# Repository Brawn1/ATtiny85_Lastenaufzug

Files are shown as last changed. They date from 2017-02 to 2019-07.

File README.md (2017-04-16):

# RF AtTiny85 gesteuerter Lastenaufzug

**Anleitung in Arbeit**

Da wir gerne Grillen aber die Sachen vom 1.OG jedesmal hinunter und 
wieder rauftragen müssen, haben wir uns entschlossen 
eine Seilwinde die noch in der Garage lag unter dem Balkon im 2.OG zu 
montieren.

Die Montage war einfach, aber leider stellte sich heraus das die 
Seilwinde sehr Langsam ist, und man die nur mit einem 2m Kabel vom 1.OG 
bedienen konnte.

Also habe ich mir überlegt dies per Microcontroller über Funk zu 
Steuern.

Da der Microcontroller keine hohe Lasten schalten kann, Steuere ich 
damit 2 Wechselrelais an.
Die Relais werden auf der 230VAC Seite so verdrahtet, dass auch bei 
einem Stecken von einem Relais immer nur eines aktiv sein kann.
Ob das jetzt das Relais für Rauf oder Runter ist kommt von der 
Sicherheit darauf an (bei mir ist es Rauf da sonst der Motor keinen
Abschaltpunkt hat).

**Tipp:**
Wenn man mehr Geld Investieren möchte, wäre ein Sicherheitsrelais 
(Schütz) dafür besser vorgesehen. Da es aber Privat ist und der 
Lastenaufzug gerade mal ca. 10x im Jahr genutzt wird, ist das nicht so 
schlimm. (über Winter wird es vom Netz getrennt).

Damit auch der Lastenaufzug vor Ort Manuell bedient werden kann, sind 
auch noch 2 Taster (Rauf, Runter) am Kasten montiert.

Da es sehr viel mit 433Mhz Fernbedinung gibt, habe ich zuerst den Code 
von der FB Ausgelesen und es in die Konditionen im Loop eingebaut.
Zum Empfangen hat sich die Lib RC-Switch am besten bewährt.

Da die Relais eher Träge sind, wird zur Sicherheit zwischen dem 
Umschalten 80ms gewartet.
Es würde zwar durch die Verdrahtung nichts machen wenn beide Relais 
aktiv sind, aber man muss es ja nicht fordern.

Kurze Funktionsvorführung

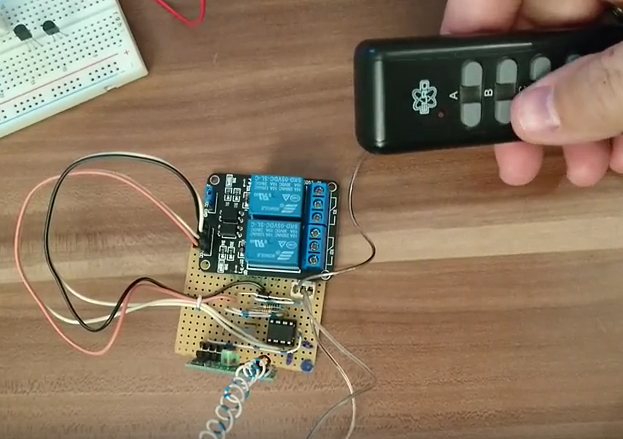
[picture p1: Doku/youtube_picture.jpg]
Funktionstest (https://youtu.be/YJzWT5fqY5Q)


Werde ein Video dazu noch nachreichen, sobald es etwas Wärmer ist. ;-)

## Benötigte Teile

* 1x 433Mhz Empfänger (E-Bay um ca. 2,50 € (Sender & Empfänger)
* 1x AtTiny85 (für die Steuerung)
* 1x Transistor PNP
* 1x 800 Ohm Widerstand
* 1x 2-Fach Relais (Bei E-Bay um ca. 5 €) *Achtung: ich habe aus 
versehen die Relais mit Optokopler gekauft, somit muss ich zum 
Abschalten der Relais die Ports auf HIGH setzen.*

## Verdrahtung

Die Verdrahtung ist dank dem AtTiny85 sehr einfach.

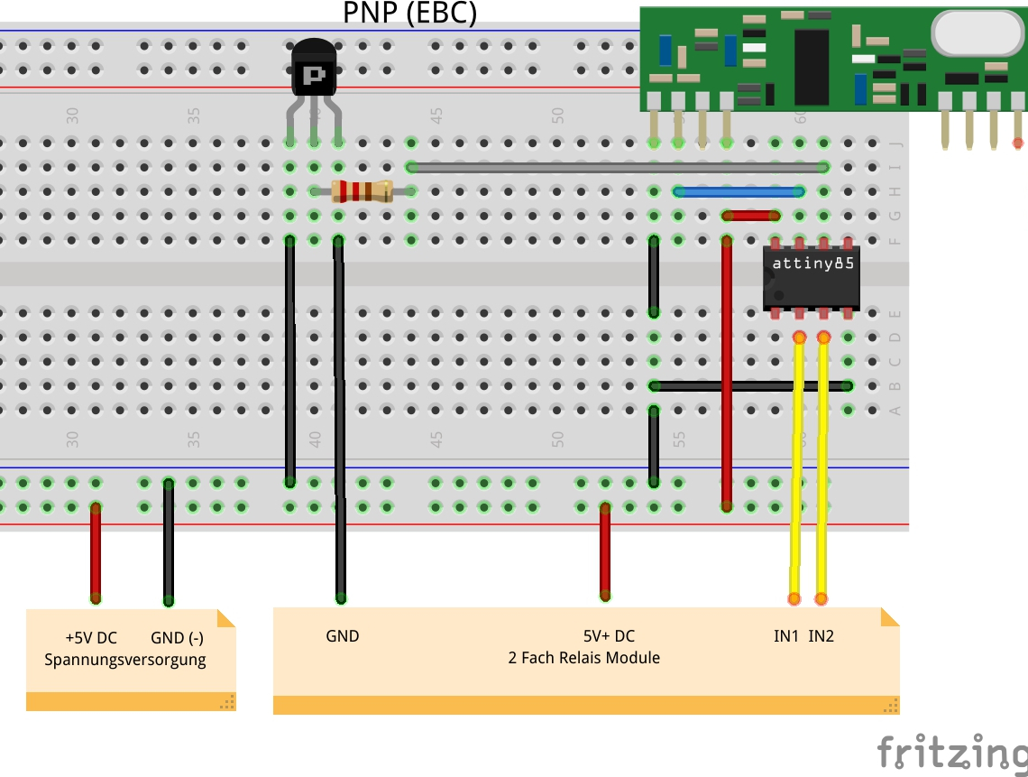
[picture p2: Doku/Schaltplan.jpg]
Verdrahtung AtTiny85

Wie man sieht verwende ich einen Widerstand von ca. 800 Ohm für den 
Transistor, somit habe ich für die Relais genau 5,5VDC.

So als Startpunkt sollte man einen 1KOhm Widerstand verwenden und es mit 
einem Multimeter nachmessen.

---

**Die Pins vom AtTiny85 werden wie dargestellt verwendet:**

---

* *PB1* -> aktivierung Spannungsversorgung vom Relais über PNP Transistor
* *PB2* -> *DATA* RF-Empfänger
* *PB3* -> *IN1* Relais 1
* *PB4* -> *IN2* Relais 2
* *VIN* -> max. 5,5 VDC
* *GND* -> GND

**433 Mhz Empfänger Aufgelötet**
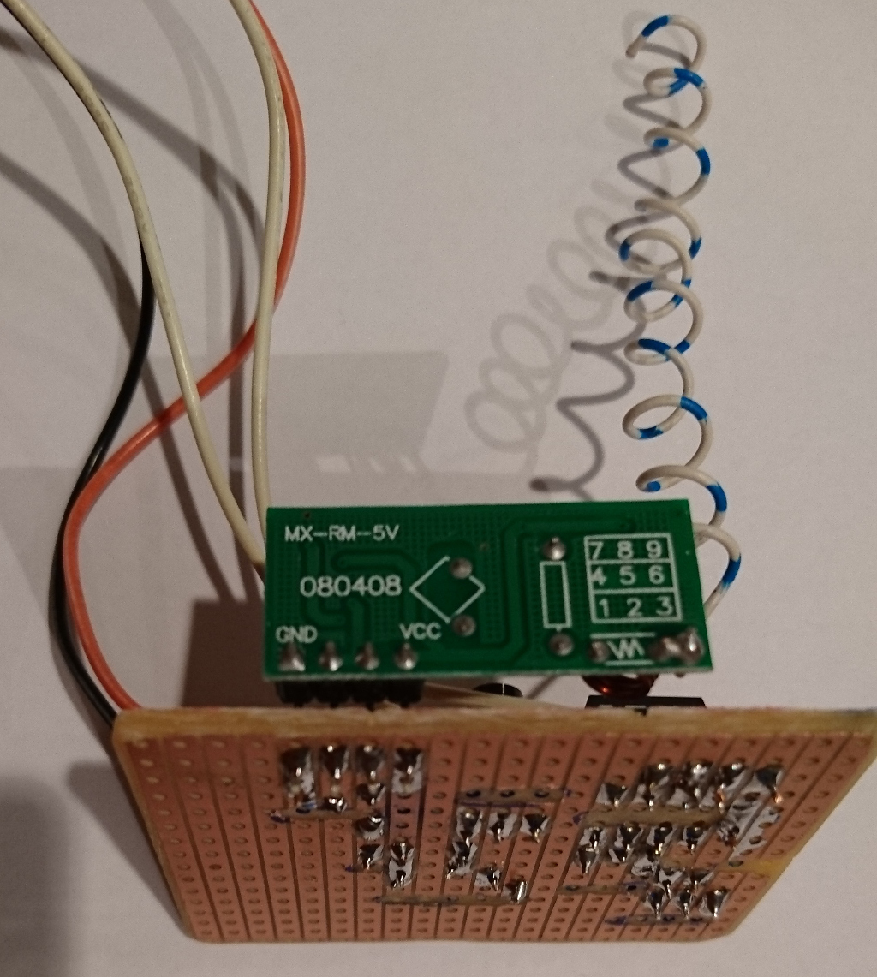
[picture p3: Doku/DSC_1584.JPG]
433Mhz Empfänger Aufgelötet


**2-Fach Relais**

**Info:** Falls eines gekauft werden muss, würde ich diese mit den 
Optokoplern nicht mehr für so ein Projekt empfehlen. 
Da nur mit *HIGH* das Relais abgeschaltet wird.
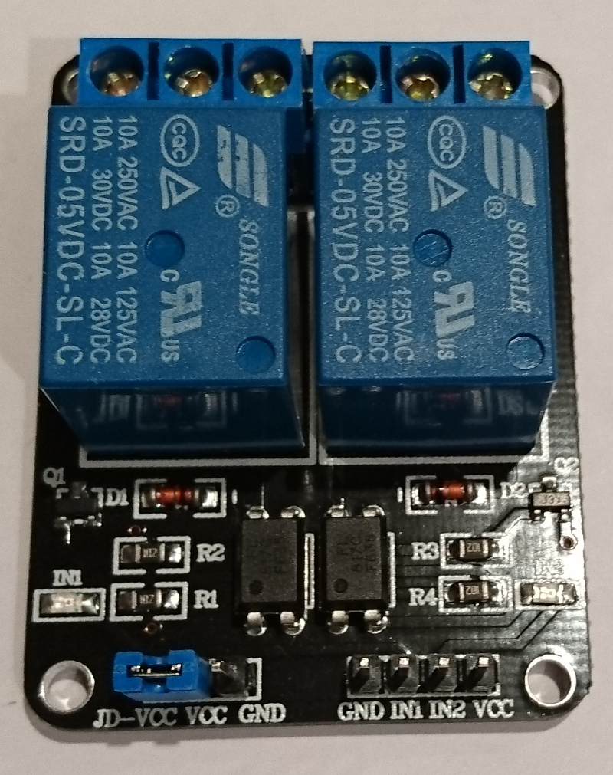
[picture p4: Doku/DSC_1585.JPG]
2-Fach Relais


**Schaltung Verdrahtet und an das Relais angeschlossen**
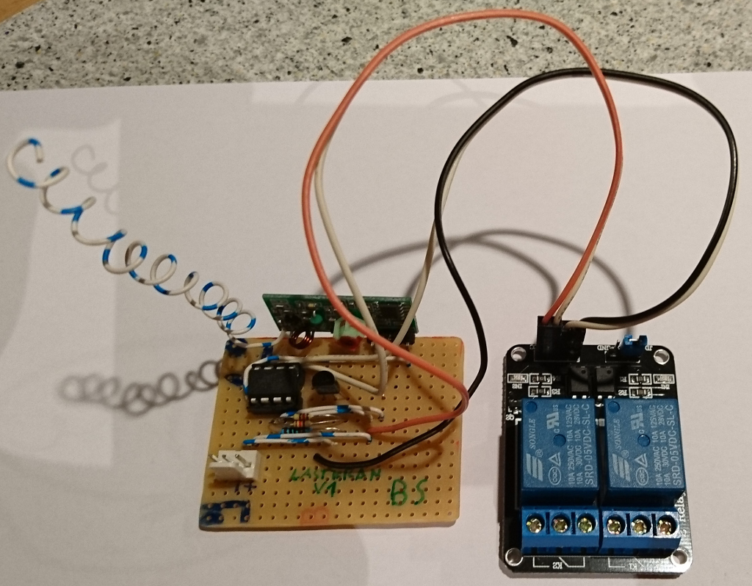
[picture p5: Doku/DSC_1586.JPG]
Schaltung Verdrahtet


## Erklärung Sketch

```Arduino
int RO = 1; // LOW = Versorge Relais (VCC) mit Spannung HIGH = schalte Spannung ab (PNP Transistor)
int S1 = 4; // Relais 1
int S2 = 3; // Relais 2
```

Da bei ATtiny85 bereits alle Pins gebraucht werden, muessen wir uns mit 
einem Boolean Feld zufrieden geben.
Die Boolean Felder sind fuer uns sozusagen der Ersatz von 2 
zusaetzlichen Input Pins.
```Arduino
boolean S1State = false;
boolean S2State = false;
boolean ROState = false;
```

Schalte die Relais Versorgungsspannung nach 1min. ab.
```Arduino
unsigned long relaistime = 60000L;
```

Wie lange das Relais den Status ON hat bis es wieder abgeschalten wird. 
Somit kann es einen bestimmten Weg zuruecklegen.
Unser Lastenaufzug schaft 6m pro Minute somit habe ich es auf 1m 
selbstfahren beschraenkt 
```Arduino
unsigned long worktime = 5000L;
```

Zur Sicherheit die Pins sofort auf HIGH setzen da das Relais mit LOW 
aktiv schaltet (Sozusagen schalten wir das Relais gleich ab).
```Arduino
void setup() {
  ...
  digitalWrite(S1, HIGH);
  digitalWrite(S2, HIGH);
  digitalWrite(RO, HIGH);
  ...
  RemoteReceiver::init(0, 0, 3, checkCode, 0); //RemoteReceiver::init(type, interrupt-pin, min-Repeats, callback-function, PulseWidth);
}
```

Aktiviere den Empfang auf den Interrupt *Pin0* => ist bei Arduino Pin2.
```Arduino
void setup() {
  ...
  ...
  RemoteReceiver::init(0, 0, 3, checkCode, 0); //RemoteReceiver::init(type, interrupt-pin, min-Repeats, callback-function, PulseWidth);
}
```

## AtTinyX5 Pins und Datenblatt

Eine kurze Darstellung der Pins vom AtTinyX5 Serie

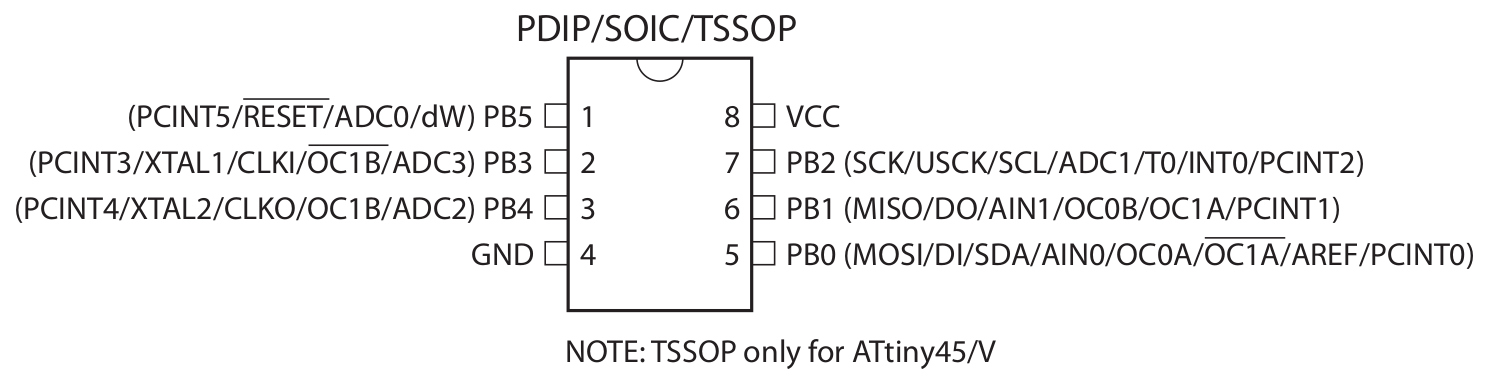
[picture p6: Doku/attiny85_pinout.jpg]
Darstellung der Pins


Das Offizielle Datenblatt von Atmel

[PDF Datasheet AtTiny25 - 85](Doku/Atmel-2586-AVR-8-bit-Microcontroller-ATtiny25-ATtiny45-ATtiny85_Datasheet.pdf)

## Quellen

* [RemoteSwitch Source](https://drive.google.com/file/d/0B4k-iADFKitTb3U0aHpLaEVqYXc/edit)
* [Atmel AtTiny85](http://www.atmel.com/devices/attiny85.aspx)
* [ATtiny Bibliothek](http://drazzy.com/package_drazzy.com_index.json)

## Erweiterung für Arduino IDE
Damit die ATtiny Serie Programmierbar mit der Arduino IDE sind, muss man die Erweiterung **http://drazzy.com/package_drazzy.com_index.json** in den Voreinstellungen hinzufügen.
Und danach bei Update das Modul aktivieren.

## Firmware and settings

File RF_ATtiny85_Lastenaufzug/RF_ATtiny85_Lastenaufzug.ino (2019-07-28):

/*
 * Lastenaufzug Steuerung mit einem ATtiny85 und einem 433Mhz Empfangsmodul.
 * 
 * Beschreibung:
 * Die Steuerung wird für einen kleinen Lastenaufzug am Balkon verwendet und muss mit einem 433MHz Sender gesteuert werden.
 * Den Sender selber haben wir zum schalten von 3 Terrassenlampen und somit haben wir noch 2 Kanäle (C,D) für unseren Lastenaufzug.
 * 
 * Da der Microcontroller keine hohe Lasten schalten kann, Steuere ich damit 2 Wechselrelais an.
 * Die Relais werden auf der 230VAC Seite so verdrahtet, dass auch bei einem Stecken von einem Relais immer nur eines aktiv sein kann.
 * Ob das jetzt das Relais für Rauf oder Runter ist kommt von der Sicherheit darauf an. (bei mir ist es Rauf da sonst der Motor keinen
 * Abschaltpunkt hat).
 * 
 * Tipp:
 * Wenn man mehr Geld Investieren möchte, wäre ein Sicherheitsrelais (Schütz) dafür besser vorgesehen. Da es aber Privat ist und der 
 * Lastenaufzug gerade mal ca. 10x im Jahr genutzt wird, ist das nicht so schlimm. (über Winter wird es vom Netz getrennt).
 * 
 * Damit auch der Lastenaufzug vor Ort Manuell bedient werden kann, sind auch noch 2 Taster (Rauf, Runter) am Kasten montiert.
 * 
 * Da es sehr viel mit 433Mhz Fernbedinung gibt, habe ich zuerst den Code von der FB Ausgelesen und es in die Konditionen eingebaut.
 * Zum Empfangen hat sich die Lib RemoteSwitch am besten bewährt.
 * 
 * Da die Relais eher Träge sind, wird zur Sicherheit zwischen dem Umschalten 80ms gewartet.
 * Es würde zwar durch die Verdrahtung nichts machen wenn beide Relais aktiv sind, aber man muss es ja nicht herausfordern.
 * 
 * 
 * ATtiny85:
 * ---------
 * VCC = 5V
 * GND = GND
 * PB1 = Transistor (PNP)
 * PB2 = DATA (433Mhz Empfänger)
 * PB3 = Relais 1 (AB)
 * PB4 = Relais 2 (AUF)
 * 
 * Info:
 * Falls ein anderer Arduino Controller verwendet wird, muss man die Pins anpassen.
 * 
 * MIT License:
 * Copyright (c) 2016 Günter Bailey
 * 
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
 * MIT Lizenz in Deutsch:
 * Copyright (c) 2016 Günter Bailey
 * 
 * Hiermit wird unentgeltlich jeder Person, die eine Kopie der Software und der zugehörigen Dokumentationen (die "Software") erhält, 
 * die Erlaubnis erteilt, sie uneingeschränkt zu nutzen, inklusive und ohne Ausnahme mit dem Recht, sie zu verwenden, 
 * zu kopieren, zu verändern, zusammenzufügen, zu veröffentlichen, zu verbreiten, zu unterlizenzieren und/oder zu verkaufen, 
 * und Personen, denen diese Software überlassen wird, diese Rechte zu verschaffen, unter den folgenden Bedingungen:
 * 
 * Der obige Urheberrechtsvermerk und dieser Erlaubnisvermerk sind in allen Kopien oder Teilkopien der Software beizulegen.
 * DIE SOFTWARE WIRD OHNE JEDE AUSDRÜCKLICHE ODER IMPLIZIERTE GARANTIE BEREITGESTELLT, 
 * EINSCHLIESSLICH DER GARANTIE ZUR BENUTZUNG FÜR DEN VORGESEHENEN ODER EINEM BESTIMMTEN ZWECK SOWIE JEGLICHER RECHTSVERLETZUNG, 
 * JEDOCH NICHT DARAUF BESCHRÄNKT. IN KEINEM FALL SIND DIE AUTOREN ODER COPYRIGHTINHABER FÜR JEGLICHEN SCHADEN ODER 
 * SONSTIGE ANSPRÜCHE HAFTBAR ZU MACHEN, OB INFOLGE DER ERFÜLLUNG EINES VERTRAGES, 
 * EINES DELIKTES ODER ANDERS IM ZUSAMMENHANG MIT DER SOFTWARE ODER SONSTIGER VERWENDUNG DER SOFTWARE ENTSTANDEN.
 * 
 */
#include <RemoteReceiver.h>

int RO = PB1; // LOW = Versorge Relais (VCC) mit Spannung HIGH = schalte Spannung ab (PNP Transistor)
int S1 = PB4; // Relais 1
int S2 = PB3; // Relais 2
/*
int RO = 4;
int S1 = 7;
int S2 = 8;
char v[4]="1.2";
*/
// da bei ATtiny85 bereits alle Pins gebraucht werden, muessen wir uns mit einem Boolean Feld zufrieden geben.
// die Boolean Felder sind fuer uns sozusagen der Ersatz von 2 zusaetzlichen Input Pins
boolean S1State=false;
boolean S2State=false;
boolean ROState=false;
// wir haben auch keinen Sensor für das erkennen in welchem Stockwerk es ist, somit werden wir auch da mit 
// Boolean Felder Raten.
boolean floor_og=false;
boolean floor_eg=false;
boolean chkfix=true;

unsigned long relaistime = 60000L; // Schalte die Relais Versorgungsspannung nach 1min. ab.
// Wie lange das Relais den Status ON hat bis es wieder abgeschalten wird. Somit kann es
// einen bestimmten Weg zuruecklegen.
// unser Lastenaufzug schaft 6m pro Minute somit habe ich es auf 2m selbstfahren beschraenkt
unsigned long worktime = 6000L;
// vom 1.OG runter in das EG braucht es ca. 17 Sekunden.
unsigned long worktimeto_eg = 17000L;

unsigned long task2 = 0;

void setup() {
  pinMode(RO, OUTPUT);
  pinMode(S1, OUTPUT);
  pinMode(S2, OUTPUT);
  // zur Sicherheit die Pins sofort auf HIGH setzen da das Relais mit LOW aktiv schaltet
  digitalWrite(S1, HIGH);
  digitalWrite(S2, HIGH);
  digitalWrite(RO, HIGH); // Pin auf HIGH Setzen
  
  RemoteReceiver::init(0, 0, 3, checkCode, 0); //RemoteReceiver::init(type, interrupt-pin, min-Repeats, callback-function, PulseWidth);

  //only for tests
  /*
  Serial.begin(115200);
  Serial.print(F("Arduino Lastenaufzug v"));
  Serial.println(v);
  Serial.println(F("=========================="));
  getboolstates();
  */
}


void SWRelais(char mode[3]){
  /*
   * Powerswitch for relais modul
   */
  if (mode == "ON") {
    if (ROState == false) {
      // Schalte Versorgungspsannung am Relais EIN
      digitalWrite(RO, LOW);
      ROState=true;
    } else if (ROState == true) {
      // do nothing
    }
  } else {
    // Sicherheitshalber bei Aufruf das Relais ausschalten
    digitalWrite(RO, HIGH);
    ROState=false;
  }
}


void SecRelais1(char mode[3]){
  /*
   * Relais 1 with state check (DOWN)
   */
  if (mode == "ON") {
    //Serial.println(F("SecRelais1 = mode ON"));
    if (S1State == false && S2State == false) {
      //Serial.println(F("SecRelais1 = ON, state = true"));
      S1State=true;
      digitalWrite(S1, LOW);
    } else if (S1State == false && S2State == true) {
      //Serial.println(F("SecRelais1 = ON, state = true"));
      digitalWrite(S2, HIGH);
      S2State=false;
      delay(80);
      S1State=true;
      digitalWrite(S1, LOW);
    } else if (S1State == true && S2State == false) {
      // do nothing
    }
  } else {
    //Serial.print(F("SecRelais1 mode = "));
    //Serial.println(mode);
    digitalWrite(S1, HIGH);
    S1State=false;
  }
}


void SecRelais2(char mode[3]) {
  /*
   * Relais 2 with state check (UP)
   */
  if (mode == "ON") {
    if (S2State == false && S1State == false) {
      //Serial.println(F("SecRelais2 = ON, state = true"));
      S2State=true;
      digitalWrite(S2, LOW);
    } else if (S2State == false && S1State == true) {
      //Serial.println(F("SecRelais1 = ON, state = true"));
      digitalWrite(S1, HIGH);
      S1State=false;
      delay(80);
      S2State=true;
      digitalWrite(S2, LOW);
    } else if (S2State == true && S1State == false) {
      // do nothing
    }
  } else {
    digitalWrite(S2, HIGH);
    S2State=false;
  }
}


//Callback function is called only when a valid code is received.
char checkCode(unsigned long receivedCode, unsigned int period){
  //Note: interrupts are disabled. You can re-enable them if needed.

  //print received code
  /*
  Serial.print("Code = ");
  Serial.println(receivedCode);
  getboolstates();
  */
  
  if (receivedCode == 531272 || receivedCode == 531363) {
    task2 = millis();
    //Serial.println("Switch Relais 1 ON");
    SWRelais("ON");
    SecRelais1("ON");
  
  } else if (receivedCode == 531380 || receivedCode == 531364) {
    //Serial.println("Switch Relais 2 ON");
    task2 = millis();
    SWRelais("ON");
    SecRelais2("ON");
  
  } else if ( receivedCode == 531276 || receivedCode == 531436 || receivedCode == 531384 || receivedCode == 531368) {
    //Serial.println("Switch Relais 1 and 2 OFF");
    SecRelais2("OFF");
    SecRelais1("OFF");
  }
}

/*
void getboolstates(){
*/
  /*
   * print all boolean states
   */
  /*
  Serial.print(F("floor_eg = "));
  Serial.println(floor_eg);
  Serial.print(F("floor_og = "));
  Serial.println(floor_og);
  Serial.print(F("S1State = "));
  Serial.println(S1State);
  Serial.print(F("chkfix = "));
  Serial.println(chkfix);
  Serial.print(F("S2State = "));
  Serial.println(S2State);
  Serial.print(F("ROState = "));
  Serial.println(ROState);
  Serial.println(F("---------------------------"));
}
*/

void loop() {
  unsigned long currmillis = millis();

  // weg von der Winde zum 1.OG
  if (floor_eg == false && floor_og == false && S1State == true) {
    /*
    if ((unsigned long)(currmillis - task2) == 2000){
      Serial.println(F("start -> 1.OG"));
    }
    */
    if ((unsigned long)(currmillis - task2) >= worktime) {
      if ( S1State == true || S2State == true ) {
        //Serial.println(F("Switch Relais after worktime OFF, start -> 1.OG"));
        SecRelais1("OFF");
        SecRelais2("OFF");
        floor_og=true;
        //getboolstates();
      }
    }
  }
  // weg vom 1.OG nach EG
  else if (floor_eg == false && floor_og == true && S1State == true) {
    /*
    if ((unsigned long)(currmillis - task2) == 2000){
      Serial.println(F("1.OG -> EG"));
    }
    */
    if ((unsigned long)(currmillis - task2) >= worktimeto_eg) {
      if ( S1State == true || S2State == true ) {
        //Serial.println(F("Switch Relais after worktime OFF, 1.OG -> EG"));
        SecRelais1("OFF");
        SecRelais2("OFF");
        floor_eg=true;
        chkfix=true;
        //getboolstates();
      }
    }
  }
  // zueruck auf das 1.OG
  else if (floor_eg == true && floor_og == true && S2State == true) {
    /*
    if ((unsigned long)(currmillis - task2) == 2000){
      Serial.println(F("EG -> 1.OG"));
    }
    */
    if ((unsigned long)(currmillis - task2) >= worktimeto_eg) {
      if ( S1State == true || S2State == true ) {
        //Serial.println(F("Switch Relais after worktime OFF, EG -> 1.OG"));
        SecRelais1("OFF");
        SecRelais2("OFF");
        floor_eg=false;
        chkfix=false;
        //getboolstates();
      }
    }
  }
  // zurueck auf start
  else if (floor_eg == false && floor_og == true && S2State == true) {
    /*
    if ((unsigned long)(currmillis - task2) == 2000){
      Serial.println(F("1.OG -> start"));
    }
    */
    if ((unsigned long)(currmillis - task2) >= worktime) {
      if ( S1State == true || S2State == true ) {
        //Serial.println(F("Switch Relais after worktime OFF, 1.OG -> start"));
        SecRelais1("OFF");
        SecRelais2("OFF");
        floor_og=false;
        //getboolstates();
      }
    }
  } 

  // steuerung weiter verwenden falls auch schon ganz unten ist
  // allerdings nur 5 Sekunden selbstfahren
  else if (floor_eg == true && floor_og == true && chkfix == true && S1State == true) {
    /*
    if ((unsigned long)(currmillis - task2) == 2000){
      Serial.println(F("Down run 5 seconds"));
    }
    */
    if ((unsigned long)(currmillis - task2) >= 5000) {
      if ( S1State == true || S2State == true ) {
        //Serial.println(F("Switch Relais after worktime OFF, run down 5 sec"));
        SecRelais1("OFF");
        SecRelais2("OFF");
        floor_eg=true;
        floor_og=true;
        chkfix=true;
        //getboolstates();
      }
    }
  }
  // steuerung weiter verwenden falls auch wenn es schon anscheinend ganz oben ist
  // allerdings nur 5 Sekunden selbstfahren
  else if (floor_eg == false && floor_og == false && chkfix == false && S2State == true) {
    /*
    if ((unsigned long)(currmillis - task2) == 2000){
      Serial.println(F("Up run 5 seconds"));
    }
    */
    if ((unsigned long)(currmillis - task2) >= 5000) {
      if ( S1State == true || S2State == true ) {
        //Serial.println(F("Switch Relais after worktime OFF, run up 5 sec"));
        SecRelais1("OFF");
        SecRelais2("OFF");
        //floor_eg=false;
        //floor_eg_fix=false;
        //getboolstates();
      }
    }
  }

  // schalte das Relais nach eingestellter Zeit aus
  if ((unsigned long)(currmillis - task2) >= relaistime) {
    if (ROState == true) {
      //Serial.println(F("interrupt Relais Power"));
      SWRelais("OFF");
      //getboolstates();
    }
  }
}

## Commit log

2017-02-01 Verschoben von Arduino Experimente in ein eigenes Repo
    [Schaltplan.fzz]
2017-04-16 Bibliothek RC-Switch entfernt
2017-04-16 Umbau von Rc-Switch auf RemoteSwitch
2017-04-16 Readme erweitert und angepasst
